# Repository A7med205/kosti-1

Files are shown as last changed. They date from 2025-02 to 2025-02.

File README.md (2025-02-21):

KOSTI-1 is a 5 DOF open-source robotic arm with a maximum payload of 500G, a reach of approximately 55cm and a total part cost of around $700; the arm lies in the mid-range between small servo arms and multi thousand dollar projects and is generally aimed towards educational and hobby purposes, but you might be able to come up with some practical ones (e.g., simple pick and place tasks, remotely turning on your coffee machine).

The manual (includes bill of material and assembly guide), .stl files, example-code and CAD files are all available for download.

*Note: The gripper displayed below is different from the updated one in the files.

[Thingiverse link](https://www.thingiverse.com/thing:6147832)

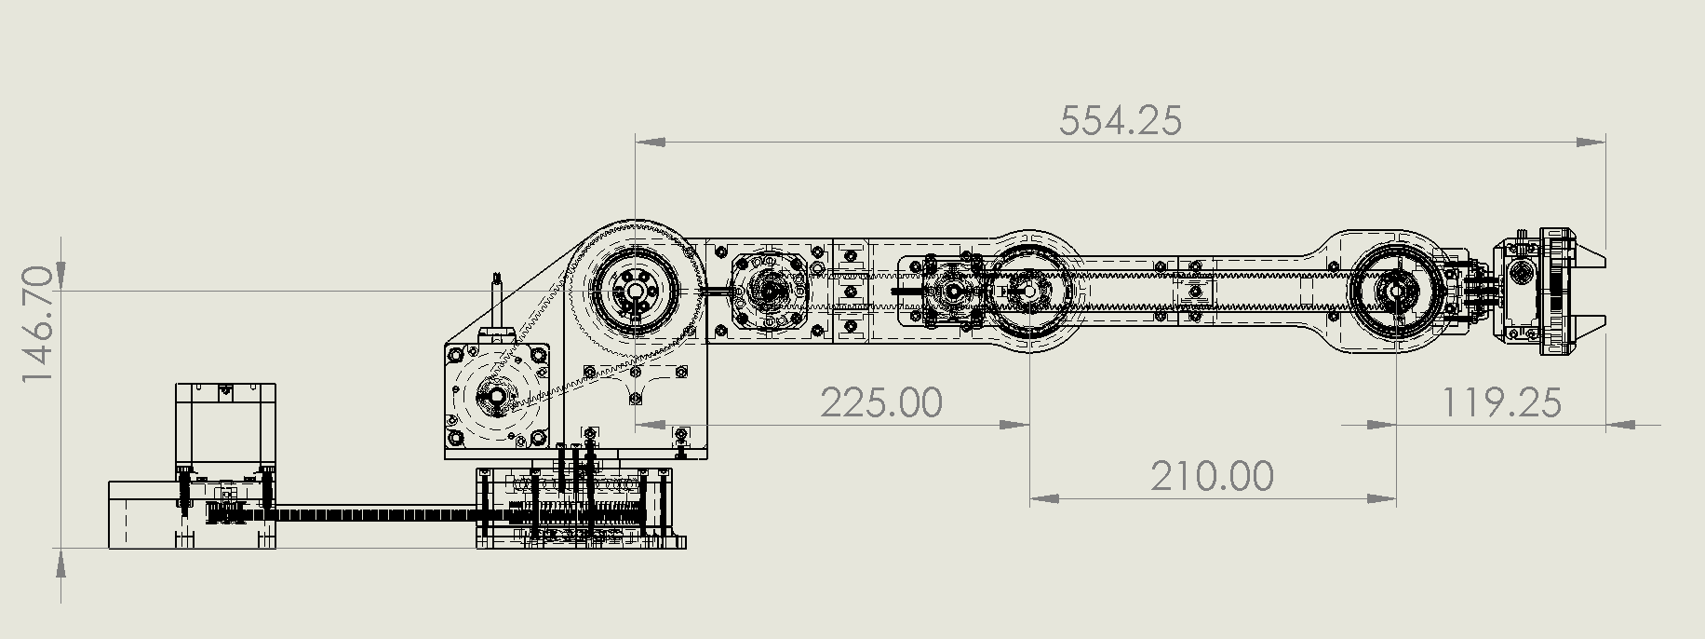
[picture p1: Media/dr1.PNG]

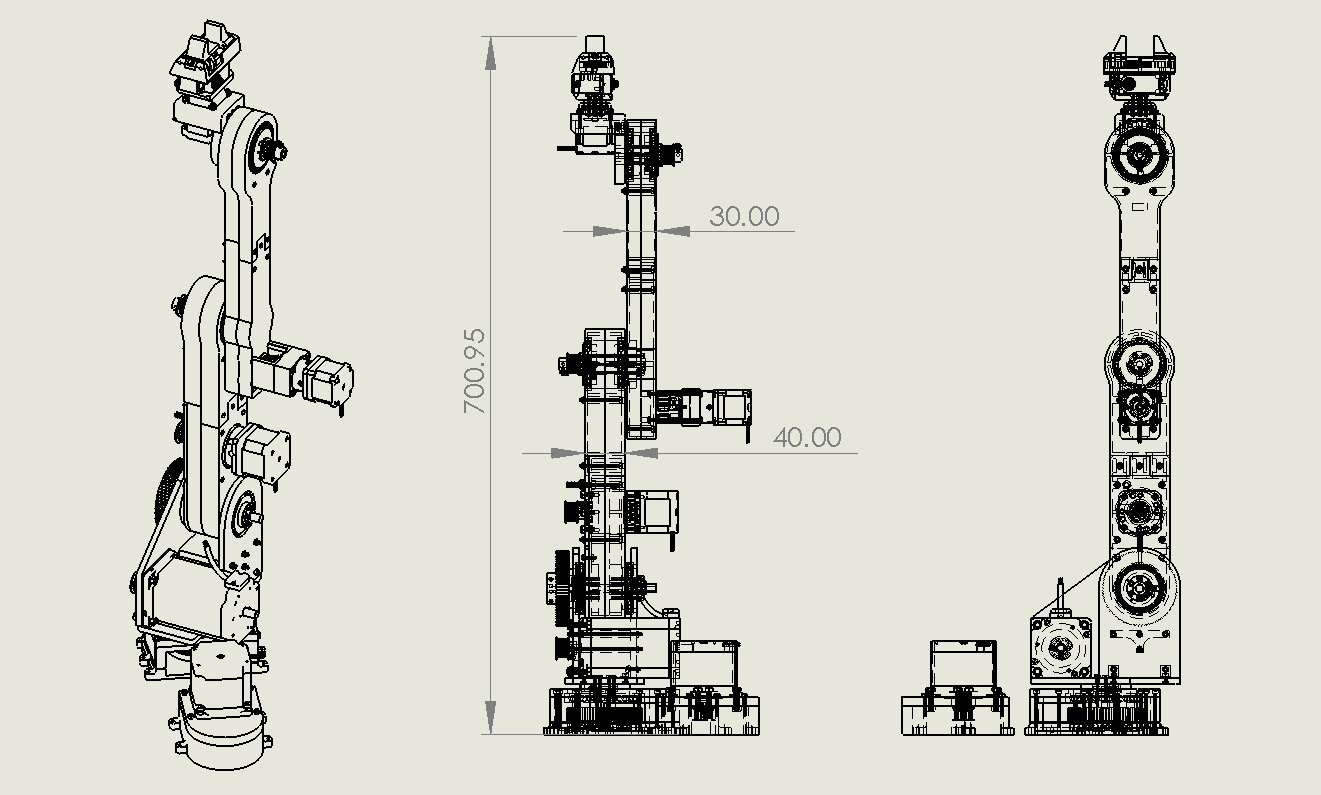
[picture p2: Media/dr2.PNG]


## Things That Might Set This Arm Apart From Other Similar Ones:

1.	Rigidity: Most parts are 3D printed, but the shoulder and base are partially made out of CNC aluminium, which adds to the rigidity of the design.
2.	Backlash: No gearbox needed for the base and shoulder joints, which means zero backlash at those joints.
3.	Smoothness: Running the shoulder and base joints at quarter step settings, combined with the fact that the remaining joints have commercial gearboxes with large resolutions, can lead to very smooth movement.
4.	Customizability: The design is entirely functional which makes it easy to modify; for instance, links can be lengthened or shortened, actuators can be replaced or modified, etc.

## Reasons Why You Might Want To Look Elsewhere:

1.	This arm isn’t entirely cost optimised; the commercial pulleys and gearboxes can be replaced with 3D printed ones or even be replaced with more affordable options, but further prototyping would be needed to achieve that.
2.	This arm is not the best choice if you want something to reliably carry out practical tasks, and there are likely commercial options out there that better suited for this.
3.	The arm uses open-loop stepper motors, and I haven’t added limit switches yet, meaning that the arm would need a pre known starting pose for every new run.

## Demo


## ROS + Moveit
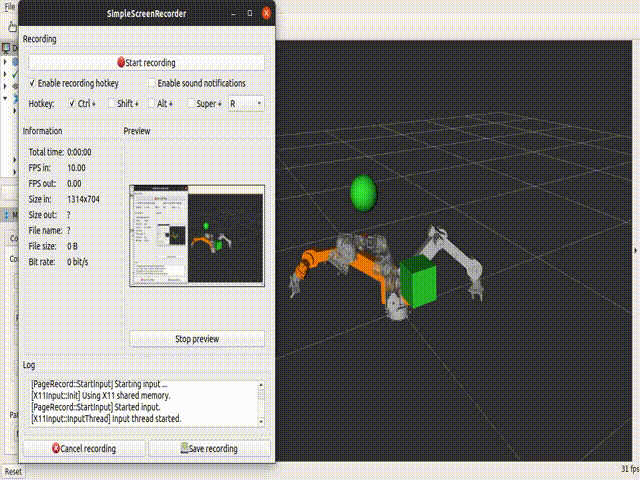
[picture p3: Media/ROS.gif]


## Assembly
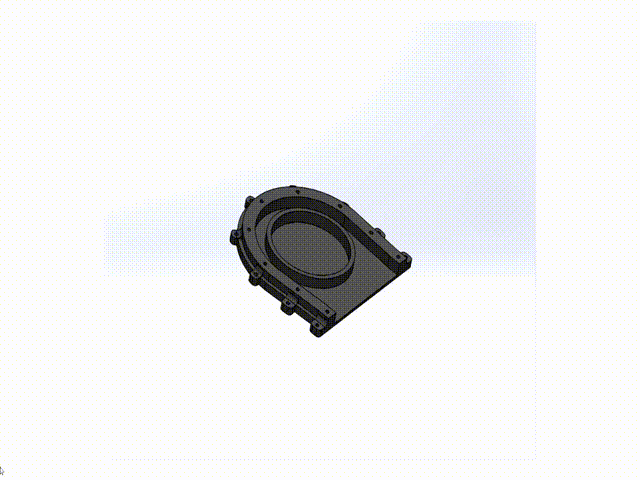
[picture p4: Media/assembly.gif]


## Exploded View
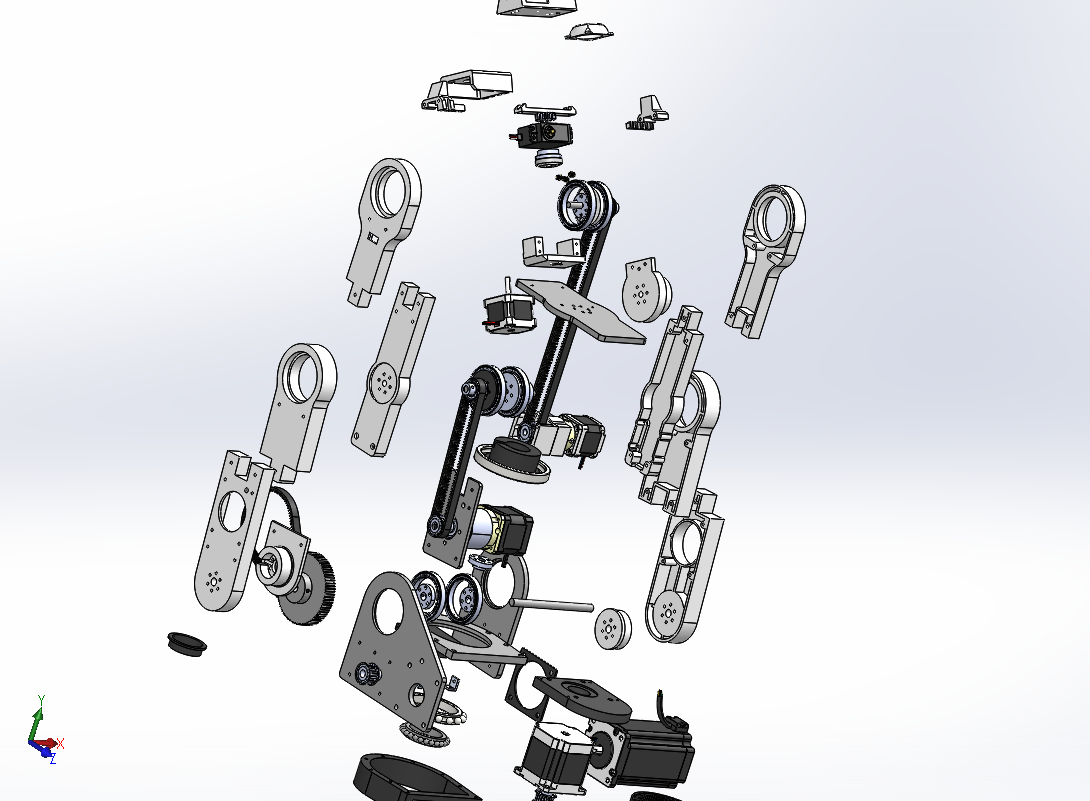
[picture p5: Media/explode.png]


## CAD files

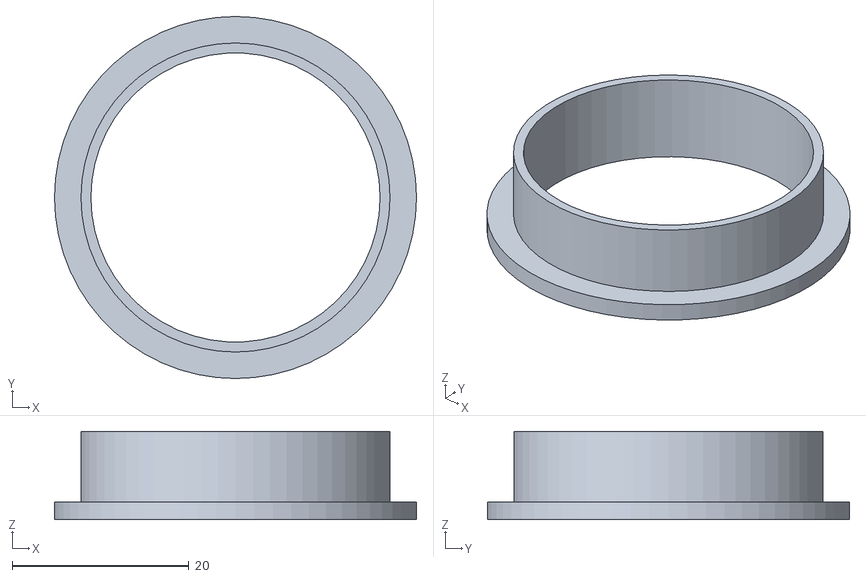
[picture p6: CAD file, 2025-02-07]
.stl files/1-stationary_base/plastic_hub.STL
41.0 x 41.0 x 10.0

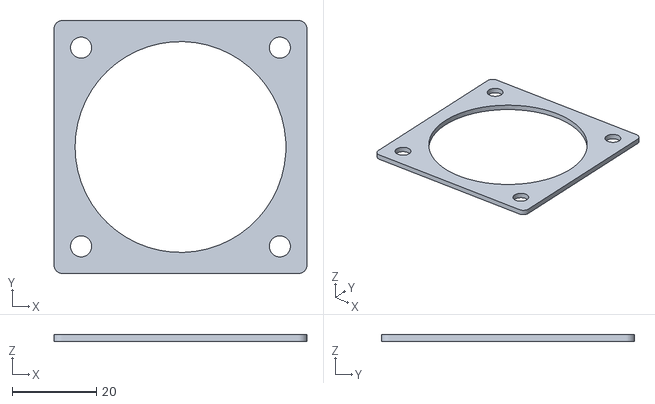
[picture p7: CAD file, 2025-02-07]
.stl files/2-rotating_base/nema24_spacer.STL
60.0 x 60.0 x 1.60

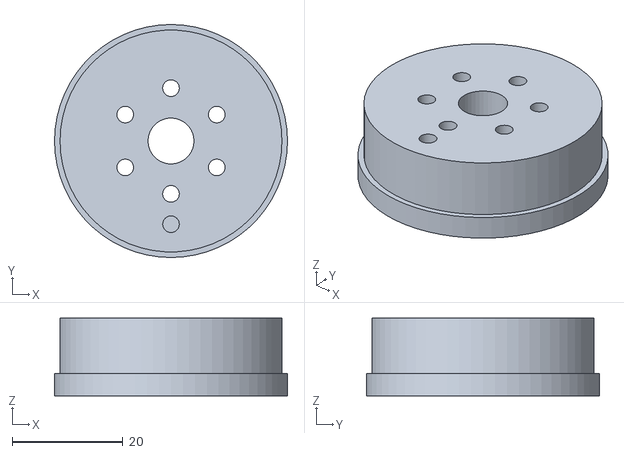
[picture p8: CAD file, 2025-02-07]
.stl files/3-lower_link/j2_hub2.STL
42.0 x 42.0 x 14.0

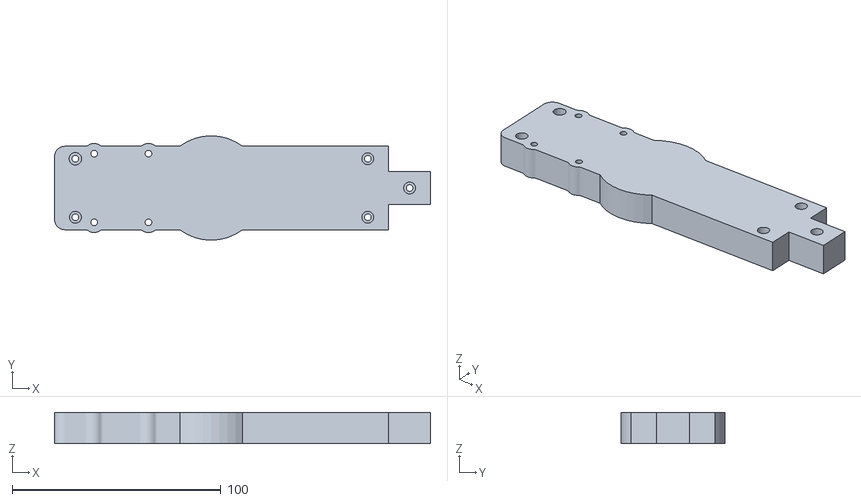
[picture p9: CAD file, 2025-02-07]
.stl files/4-middle_link/upper_arm_right_1.STL
180.0 x 50.0 x 15.0

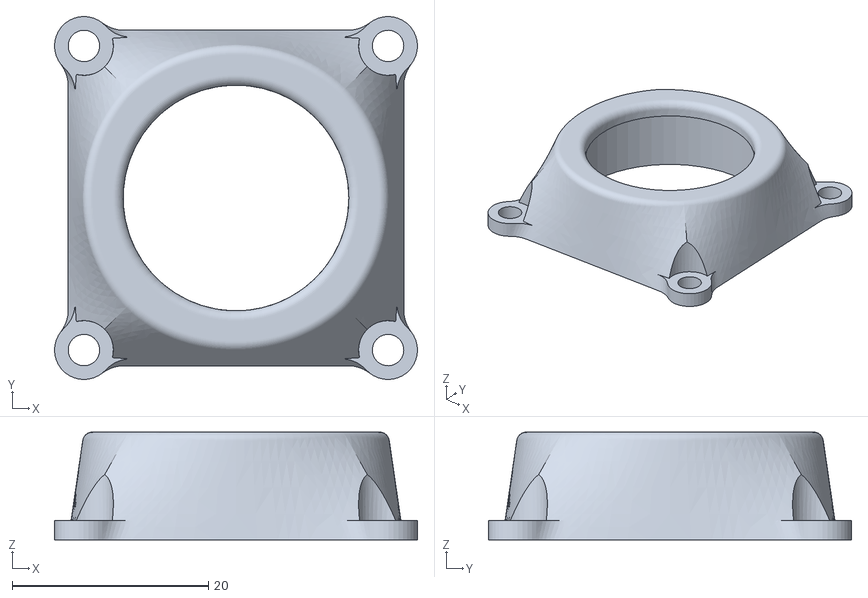
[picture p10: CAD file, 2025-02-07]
.stl files/5-third_link/bearing_housing.STL
37.0 x 37.0 x 11.0

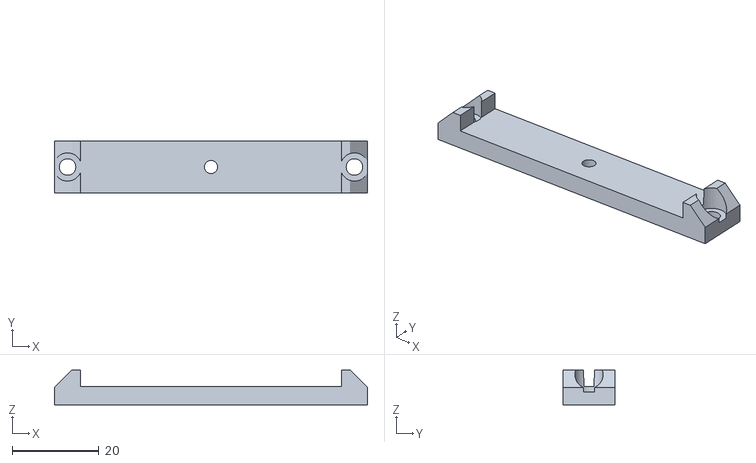
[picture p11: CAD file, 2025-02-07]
.stl files/6-end_effector_SG1/SG1_center_bar.STL
72.0 x 12.0 x 8.02

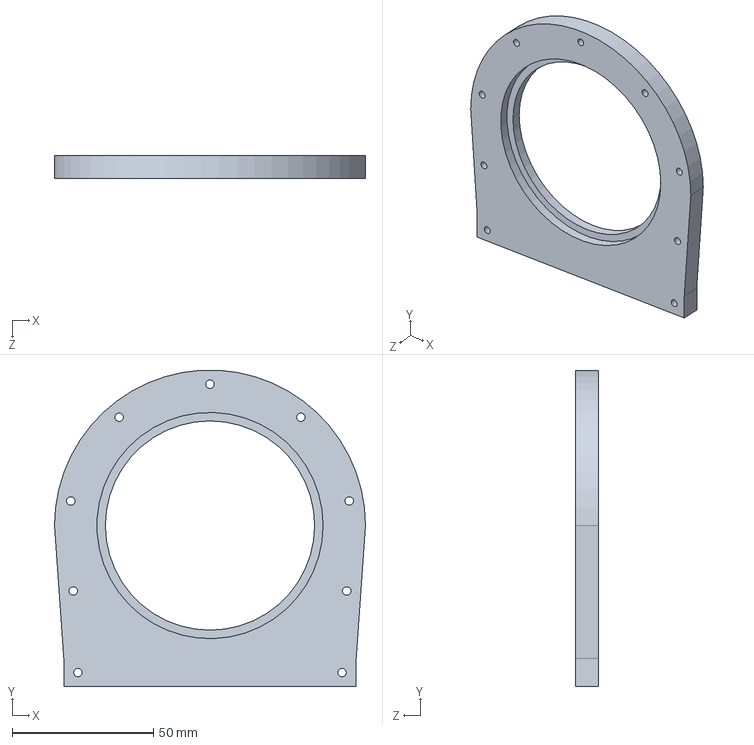
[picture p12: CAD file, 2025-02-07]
Aluminium Parts/aluminum base.SLDPRT
110.0 x 111.9 x 8.00 mm

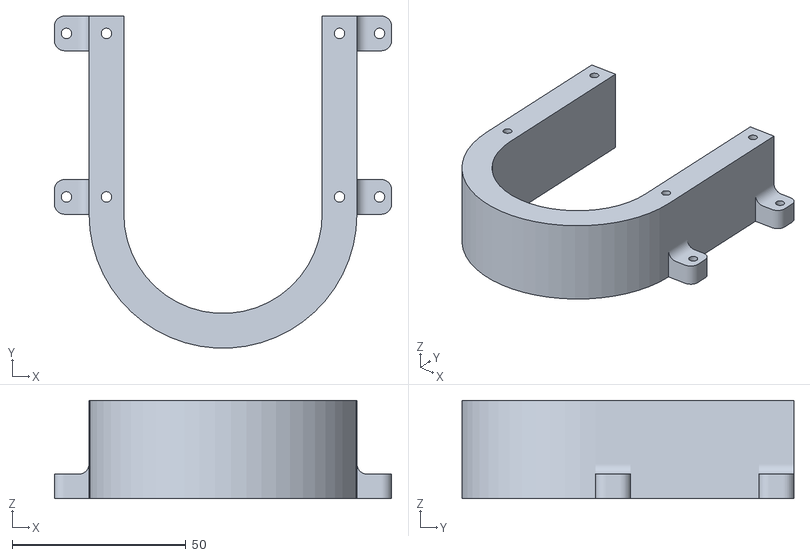
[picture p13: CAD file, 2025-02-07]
.stl files/1-stationary_base/j1_2.STL
97.0 x 95.4 x 28.2

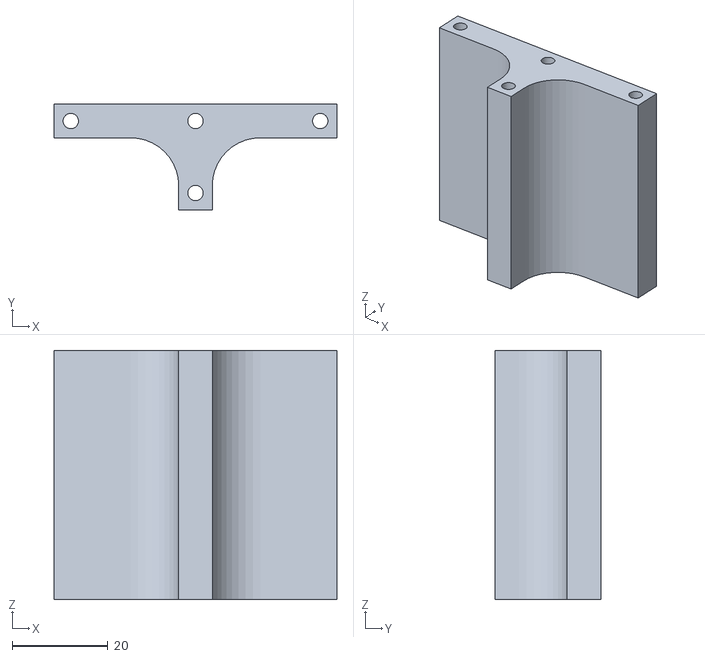
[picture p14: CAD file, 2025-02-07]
.stl files/2-rotating_base/support.STL
59.0 x 22.0 x 52.0

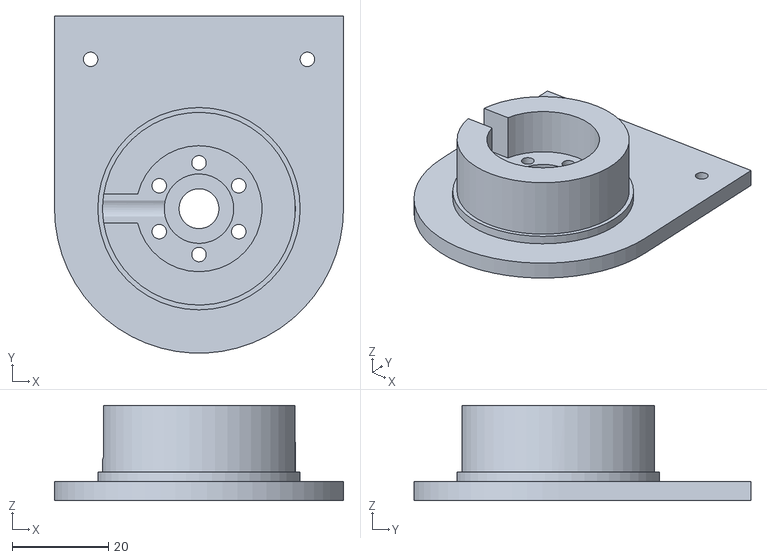
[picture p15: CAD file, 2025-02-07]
.stl files/3-lower_link/j2_hub1.STL
60.0 x 70.0 x 19.8

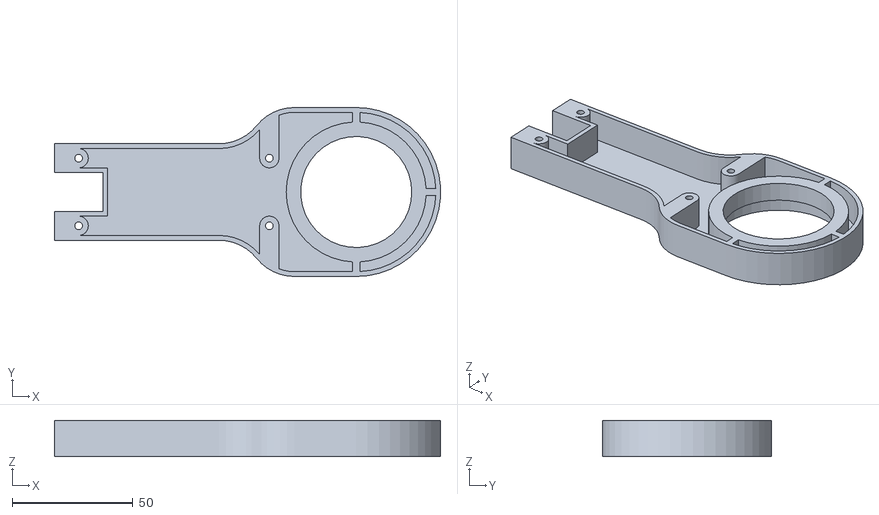
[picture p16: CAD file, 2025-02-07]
.stl files/4-middle_link/upper_arm_right_2.STL
159.9 x 70.0 x 15.0

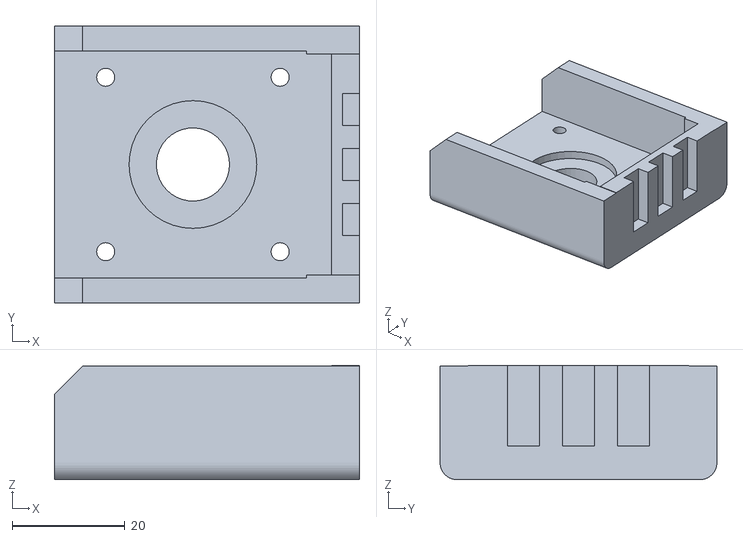
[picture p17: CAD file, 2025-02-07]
.stl files/5-third_link/link3.STL
54.2 x 49.2 x 20.3

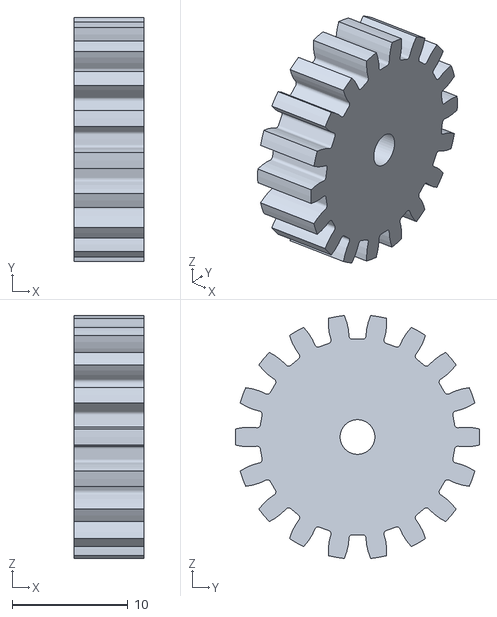
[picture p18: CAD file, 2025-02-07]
.stl files/6-end_effector_SG1/SG1_gear.STL
6.00 x 21.1 x 21.0

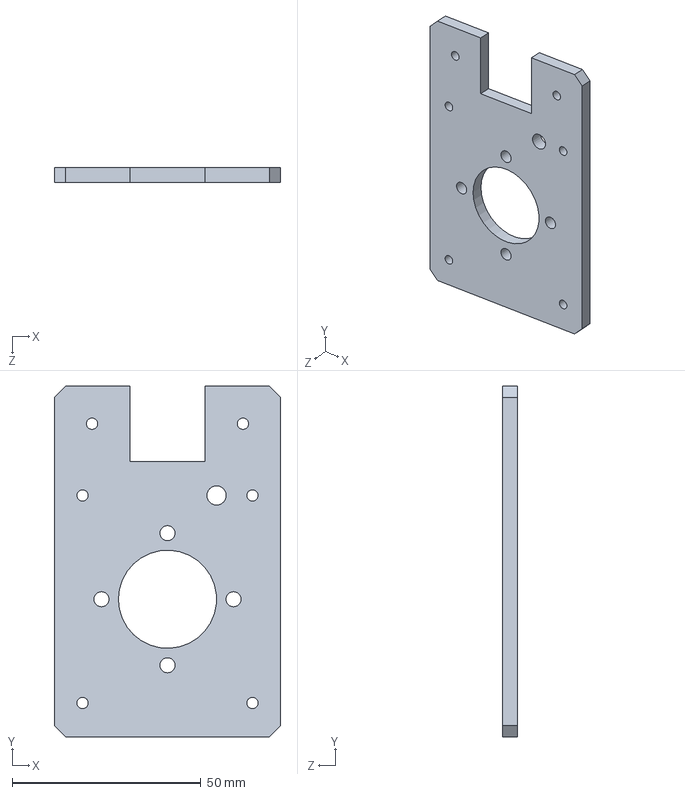
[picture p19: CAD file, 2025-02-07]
Aluminium Parts/j3_plate.SLDPRT
60.0 x 93.0 x 4.00 mm

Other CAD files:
.stl files/1-stationary_base/j1_1.STL
.stl files/2-rotating_base/j1_hub.STL
.stl files/3-lower_link/lower_arm_right_2.STL
.stl files/4-middle_link/j4_mount_2.STL
.stl files/1-stationary_base/ground.STL
.stl files/1-stationary_base/stationary_base.STL
.stl files/3-lower_link/lower_arm_left_1_.STL
.stl files/3-lower_link/lower_arm_left_2.STL
.stl files/3-lower_link/lower_arm_right_1_.STL
.stl files/4-middle_link/J3_hub_2.STL
.stl files/4-middle_link/clamp.STL
.stl files/4-middle_link/clamp2.STL
.stl files/4-middle_link/j3_hub.STL
.stl files/4-middle_link/j4_mount.STL
.stl files/4-middle_link/upper_arm_left_1_.STL
.stl files/4-middle_link/upper_arm_left_2.STL
.stl files/5-third_link/bearing_housing_2.STL
.stl files/5-third_link/end_effector_hub.STL
.stl files/5-third_link/end_effector_hub2.STL
.stl files/5-third_link/j4_hub1.STL
.stl files/5-third_link/j4_hub2.STL
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

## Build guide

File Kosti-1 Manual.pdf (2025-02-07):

## KOSTI-1 Manual

# Kosti-1 Manual

Features:

Kosti-1 is a 5 degree of freedom open-source robotic arm with a maximum payload of 500gm (including the end-effector) and a reach of approximately 55cm. The total part cost is around $700 in addition to machining and shipping costs.

The body of the arm requires both 3D-printed parts and aluminium parts that need to be machined and can’t be omitted without significant design changes. All joints are driven by open-loop stepper motors, and 4 out of 5 of these joints have a timing belt and pulley drive for load reduction and/or power transmission. This manual includes schematics and examples for Arduino based control, but different methods of control can be employed.

CONTENTS:

- 3D Printing
- CNC Machining
- Post Machining
- Arm Platform
- Tools
- Fits and Tolerances
- Belt Tensioning
- End Effector
- Bill of Materials
- Assembly Guide
- Stepper Motor Wiring
- Servo Gripper Wiring

3D Printing the Parts:

Printer: All parts can fit inside a 220x220mm printer.

Filament: The design of the plastic parts assumes a shrinkage rate of no more than 2-3%, which is common for PLA, take that into consideration if you end up using another type of filament and consider printing a single piece first to check the fits before proceeding with the rest.

Printer settings: All parts were printed using 0.2mm layer, height and 20-25% infill and two outer shells; increasing the number of shells can add rigidity but would add to the weight. Make sure that you pick the print orientation that minimizes support material for each part.

CNC Machining:

There are 5 parts that need to be machined out of aluminium plate(s) using a CNC machine; the 3 maximum dimensions for each part are (131 x 82 x 6mm), (131 x 148.17 x 6mm), (150.20 x 64 x 6mm), (112 x 110 x 8mm) and (93 x 60 x 4mm), you can use these dimensions to select the stock plate.

Post Machining:

Shafts: An 8mm shaft needs to be cut into an 8x47mm one and an 8x110 one, and a 6mm shaft needs to be cut into a 6x95mm one and a 6x64mm one. A 0.5mm flat should be filed onto the 8x110mm and 6x95mm shafts for more secure joints, and optionally, the same can be done for the other two shafts.

Pulleys: The bore on two out of the six small pulleys needs to be increased in diameter from 6mm to 8mm to match the motor shafts, and ideally, a lathe would be used to do this, similar to what’s done here. (https://www.youtube.com/watch?v=ZHTQ478ji7k) Other methods can be used with less precise results.

Threaded Rods: Four M3x75mm and four M3x55mm threaded rods need to be cut out of standards lengths ones.

M5 Screws: If narrow head M5 screws are not available, eight hex head ones can be filed to fit on the back of the face of the Nema24 and Nema23 motors.

‘link3’: Three M3 clearance holes need to be drilled into this part, see step NO. 36.

Platform: You are likely going to need to prepare some sort of platform, usually out of wood, to secure the base of the arm onto.

Tools:

The tools you need would depend, in some cases, on your preferred method of machining; you might want to cut the shafts with a hacksaw or a circular saw, you might have a mill for filing the flats or you might just use a file and a vise, and you might have a lathe for boring the pulleys or you might use a drill with a reamer bit. You will need a soldering iron, 1.5mm, 2mm and 2.5mm Allen keys, and some pliers.

Fits and Tolerances:

The CAD files included for aluminium parts have bearing and screw holes that simply match the nominal diameters of the ready parts, these can be edited to achieve the desired fit.

The bearing and screw-clearance holes on the 3D printed parts assume a shrinkage rate of 2-3%, if the fit on the test piece fails one way or the other, the .stl file can be slightly scaled up or down using the slicing application; make sure that use uniform scaling.

The screw holes on the printed parts match the diameter of the screw shafts and should shrink enough for the screws to self-tap into.

Belt Tensioning:

Base joint: The base is split into two fixed parts connected only by the belt; these two parts can be manually set apart and secured to the platform with a distance that ensures that the belt is properly tensioned.

Shoulder joint: The centre distance required for good tension between each two pulleys can be calculated using the provider’s online tool, and the centre distance on the aluminium plate holding the two pulleys for the shoulder joint is 1% larger than the calculated one, which would result in good tension at installation without the need for a tensioner, assuming that the specified closed loop belt and pulleys are selected. In any case, a clearance hole for an M5 screw is present on the plate behind where the belt should be, and that hole can be used to add a tensioner similar the one included for the elbow joint and explained below.

Elbow joint: There’s no easy way to predict the resulting centre distance on 3D printed parts, and proper tension can be hard to achieve, even when allowance is made for shrinkage, without some sort of adjustable tensioner;
the tensioner for the elbow joint is | simply two 5mm bore bearings with a
thickness of 5mm held on an M5 | screw and secured with nuts on both sides, the
thickness of the bolt below the | bearings can be filed down if they’re too high
and a spacer can be added if they’re | too low, and the tension can be adjusted by
either 3D printing a small hollow | cylinder that goes over the bearings or by
using bearings with a larger outer | diameter. See assembly step NO. 13.

Wrist Joint: The second link where the wrist joint belt is attached wasn’t designed to hold a screw based tensioner, and I currently don’t have access to the assembly to test another tensioner design, consequently, the recommended method for tensioning the upper most belt is cutting it and attaching the two ends with two clamps (.stl included), a screw and a nut. The wrist joint should have more than the sufficient range of motion without the clamp reaching either pulley, but you’re free to come up with other ways for tensioning this belt.

End Effector:

The end effector included is the open-source gripper from Anninrobotics.com; the assembly manual and bill of materials for the servo gripper are separately available at anninrobotics.com/downloads under ‘Servo Gripper’, but the printable files have been adjusted to fit onto the different hub and can be found with the rest of Kosti-1’s files. Note that the same servo is included in both Kosti-1’s BOM and the BOM for the gripper while you will only need one servo.

Bill of Materials:

NO. | PART NAME | QTY. | NOTE | LINK
| Belts & Pulleys
1 | 80T Pulley, 3 mm Pitch, 8mm Bore | 2 | | Link (https://shop.sdp-si.com/catalog/product/?id=A_6A53M080NF0908)
2 | 20T Pulley, 3 mm Pitch, 6mm Bore | 6 | | Link (https://shop.sdp-si.com/catalog/product/?id=A_6A53M020DF0906)
3 | 184T, 3mm pitch, 9mm width Belt | 1 | | Link (http://shop.sdp-si.com/catalog/product/?id=A%206R53M184090)
4 | 119T, 3mm pitch, 9mm width Belt | 1 | | Link (http://shop.sdp-si.com/catalog/product/?id=A%206R53M119090)
5 | 118T, 3mm pitch, 9mm width Belt | 1 | | Link (http://shop.sdp-si.com/catalog/product/?id=A%206R53M118090)
6 | 187T, 3mm pitch, 9mm width Belt | 1 | | Link (http://shop.sdp-si.com/catalog/product/?id=A%206R53M187090)
| Motors
7 | Nema24 4.2A 4Nm | 1 | | Link (https://www.omc-stepperonline.com/dual-shaft-nema-24-stepper-motor-4-2a-4nm-566-oz-in-60x60x100mm-4-wires-24hs39-4204d)
8 | Nema23 2.8A 1.26Nm | 1 | | Link (https://www.omc-stepperonline.com/nema-23-bipolar-1-26nm-178-4oz-in-2-8a-2-5v-57x56mm-4-wires-6mm-shaft-23hs22-2804s1)
9 | Nema17 Geared | 1 | | Link (https://www.omc-stepperonline.com/nema-17-stepper-motor-l-40mm-gear-ratio-20-1-mg-series-planetary-gearbox-17hs15-1584s-mg20)
10 | Nema14 Geared | 1 | | Link (https://www.omc-stepperonline.com/nema-14-stepper-motor-bipolar-l-33mm-w-gear-ratio-19-1-planetary-gearbox-14hs13-0804s-pg19)
11 | Nema16 | 1 | | Link (https://www.omc-stepperonline.com/nema-16-bipolar-1-8deg-21ncm-29-7oz-in-0-4a-12v-39x39x34mm-4-wires-16hs13-0404s)
| Electronics
12 | Servo | 1 | | Link (https://www.amazon.com/ANNIMOS-Digital-Waterproof-Crawler-Control/dp/B07GK1G5FV?amp;keywords=25kg+servo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)
13 | arduino | 1 | | Link (https://www.amazon.com/ELEGOO-ATmega2560-ATMEGA16U2-Arduino-Compliant/dp/B01H4ZDYCE?amp;keywords=arduino%252Bmega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)
14 | jumper wires | 35 | | Link (https://www.amazon.com/sspa/click?linkId=0729893a4c66a6ac7699d003874922f6&camp=1789&creative=9325)
15 | bread board | 1 | | Link (https://www.amazon.com/Pcs-MCIGICM-Points-Solderless-Breadboard/dp/B07PCJP9DY?amp;keywords=breadboard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)
16 | extension wires | 8 | | Link (https://www.omc-stepperonline.com/stepper-motor-4-wires-400mm-cable-with-pitch-connector-c001)
17 | DM54T driver | 2 | | Link (https://www.omc-stepperonline.com/digital-stepper-driver-1-0-4-2a-20-50vdc-for-nema-17-23-24-stepper-motor-dm542t)
18 | DM320T driver | 3 | | Link (https://www.omc-stepperonline.com/digital-stepper-driver-0-3-2-2a-10-30vdc-for-nema-8-11-14-16-17-stepper-motor-dm320t)
19 | 400W 24V power supply | 1 | | Link (https://www.omc-stepperonline.com/nema-16-bipolar-1-8deg-21ncm-29-7oz-in-0-4a-12v-39x39x34mm-4-wires-16hs13-0404s)
| Bearings
20 | 35x62x9mm_bearing_16007 | 1 | | Link (https://www.amazon.com/16007-Bearing-grove-bearing-Radial/dp/B07LB84RHP?amp;keywords=35x62x9+bearing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)
21 | 50x80x10mm_bearing_16010 | 1 | | Link (https://www.amazon.com/16010-Open-Bearing-50x80x10-Shipping/dp/B083QPRJZ6?amp;keywords=50x80x10+bearing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)
22 | 40x52x7mm_bearing_6808-2RS | 6 | | Link (https://www.amazon.com/XIKE-6808-2RS-Bearings-40x52x7mm-Pre-Lubricated/dp/B09D2VY3BK?amp;keywords=40x52x7%252Bbearing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)
23 | 20x27x4mm_bearing_6704ZZ | 1 | | Link (https://www.amazon.com/uxcell-6704ZZ-Groove-Bearings-Shielded/dp/B082PSMMGV?amp;keywords=20x27x4mm%252Bbearing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)
24 | 5mm ID 5mm thick bearing | 2
| Fastners, Shafts & Hubs
25 | M3 x 0.5 x 10 Hex | 6 | | Link (https://www.amazon.com/Assortment-Stainless-Replacement-Machine-Fastener/dp/B0BMQFHDBH?amp;keywords=M3+Hex+Cap+Screws+set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)
26 | M3 x 0.5 x 35 Hex | 9
27 | M3 x 0.5 x 12 Hex | 6
28 | M3 x 0.5 x 8 Hex | 8
29 | M3 x 0.5 x 25 Hex | 14
30 | M3 x 0.5 x 5 Hex | 12
31 | M3 x 0.5 x 40 Hex | 12

32 | M3 x 0.5 x 30 Hex | 19
33 | M3 x 0.5 x 20 Hex | 8
34 | M3 x 0.5 x 16 Hex | 4
35 | M3 x 0.5 x __ Hex | 13 + 12
36 | Hex nut, M3 x 0.5 | 42 + 13 + 12
37 | M4 x 0.7 x 10 | 4
38 | M5 screw x 0.8 x 20 | 8 | Link (https://www.amazon.com/Kadrick-Assortment-Metric-Washers-Upgrade/dp/B0BZ6NVQZP?amp;qid=1689360725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)
39 | M5 screw x 0.8 x 25 | 1
40 | M5 nut, M5 x 0.8 | 10
41 | Corner Bracket | 4 | Link (https://www.mcmaster.com/1959N41/)
42 | Threaded rod M3 x 0.5 x (75 + 55) | 4 | Link (https://www.amazon.com/uxcell-130mm-Threaded-Stainless-Threads/dp/B094H9VQDB?amp;qid=1689358986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)
43 | M3 Insert | 3 | Link (https://www.amazon.com/Printing-M3x4x5mm-Threaded-Embedment-Automotive/dp/B0BTYF2MMD?amp;qid=1689358986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)
44 | Shaft 1, 2_8 x (47+110) | 1 | Link (https://www.amazon.com/uxcell-200mm-Stainless-Steel-Solid/dp/B082ZNFMXV?amp;qid=1689353881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)
45 | Shaft 3, 4_6 x (95 +64) | 1 | Link (https://www.amazon.com/6mmX100mm-Linear-Motion-Shaft-Diameter/dp/B08HYF2WPX?amp;keywords=6mm%252Bshaft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)
46 | 8mm hub | 3 | Link (https://www.pololu.com/product/2693)
47 | 6mm hub | 3 | Link (https://www.pololu.com/product/1999/)
48 | 5mm hub | 1 | Link (https://www.pololu.com/product/1998)
*Some of these are affiliate links.
*You can source the same parts from any preferred distributer.

Assembly Guide:
*Some parts are supressed when they’re not the focus of a given step.

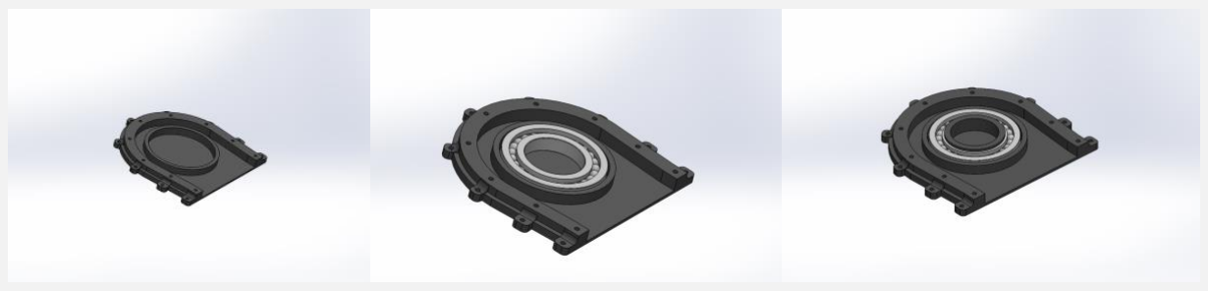
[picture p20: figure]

1. Insert the 35mm bore bearing into the piece making the bottom of the base and insert the ‘plastic_hub’ piece into the bearing; the bearing should have a slide fit.
2. Insert the 8x47mm shaft into the 8mm aluminium hub, making sure that the end of the shaft is flat with the surface of the hub and secure the shaft to the hub using the M3x10mm socket head screw instead of the set screw. Install the remaining hub set screw normally.

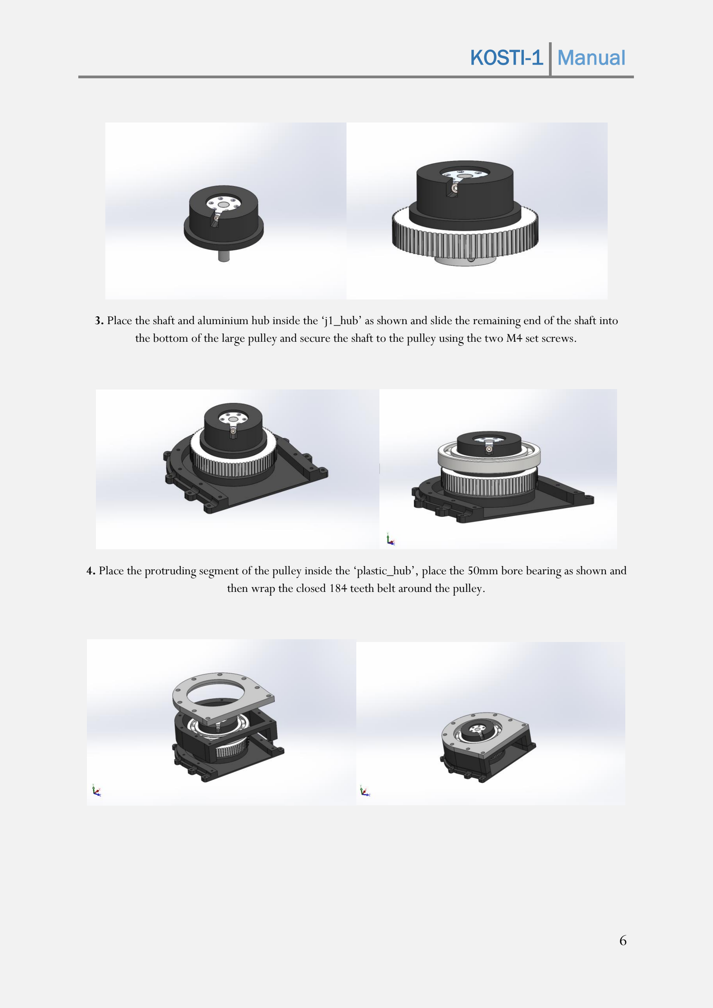
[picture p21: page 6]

3. Place the shaft and aluminium hub inside the ‘j1_hub’ as shown and slide the remaining end of the shaft into the bottom of the large pulley and secure the shaft to the pulley using the two M4 set screws.
4. Place the protruding segment of the pulley inside the ‘plastic_hub’, place the 50mm bore bearing as shown and then wrap the closed 184 teeth belt around the pulley.

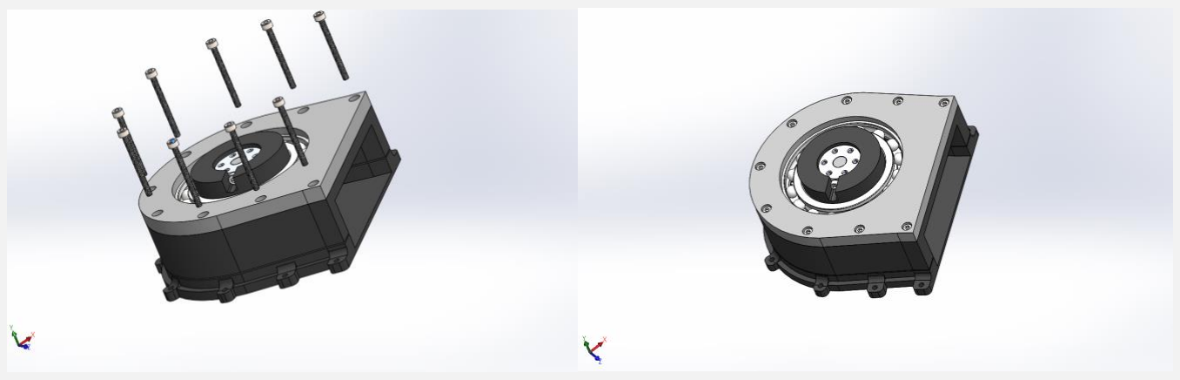
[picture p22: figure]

5. Complete the base by placing the two remaining plastic and aluminium pieces over the large bearing as shown and screwing everything using 9 M3x35mm socket head screws; the bearing should have a slide fit; note that the screws should self-tap into the bottom piece.
6. Secure the aluminium ‘base_plate’ and ‘left-plate’ using two corner brackets, two M3x12mm screws, two M3x8mm screws and 4 M3 nuts; note that the longer screws go into the side plate and that the longer side of the bracket should be the vertical one.

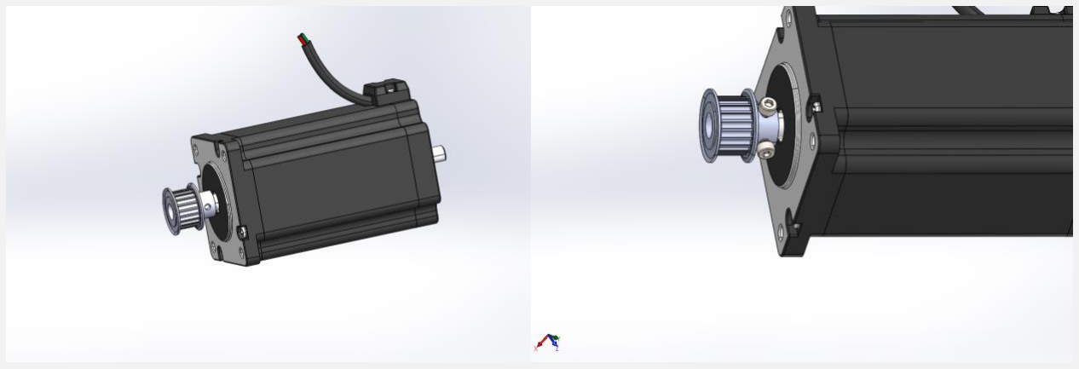
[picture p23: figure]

7. Secure the small 8mm bore onto the Nema24 motor using two 5mm screws, making sure that screws are pressing on the flat sides of the shaft and that the pulley is as close to the body of the motor as possible without the screws leaving the flat sides.

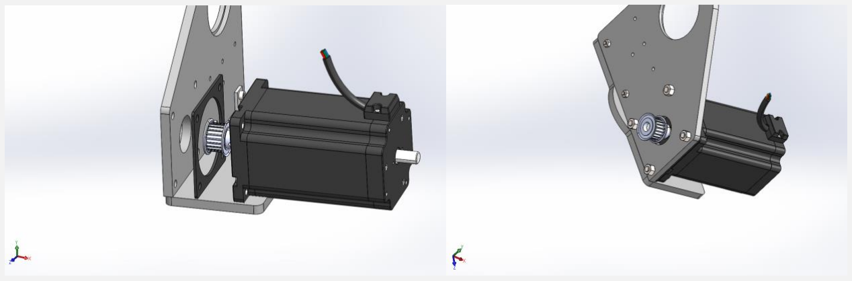
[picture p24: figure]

8. Secure the Nema24 motor to the side plate, through the spacer, using 4 M5x20mm screws and 4 M5 nuts.
9. Secure the plates and the motor to the base using 6 M3x25mm screws; the screws should go through the threaded 8mm hub below and self-tap into the plastic, so make sure that the 6 holes on the hub and plate are properly aligned.

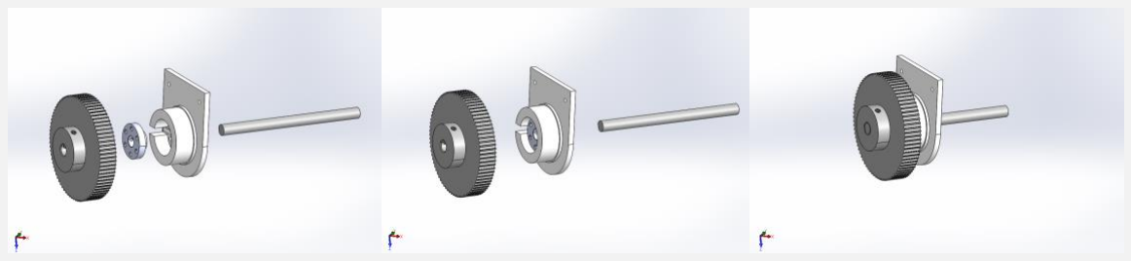
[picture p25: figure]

10. Insert the 8mm aluminium hub into ‘j2_hub1’ as shown, with the set screw holes facing the removed part of the plastic cylinder, and slide the 8x110mm shaft through a large pulley that’s held flat against ‘j2_hub1’, making sure that the end of the shaft is flat with the surface of the pulley. The pulley shouldn’t be secured yet and is only needed to mark the shaft distance.
11. Secure the shaft to the hub using an M3x10mm screw and remove the pulley.

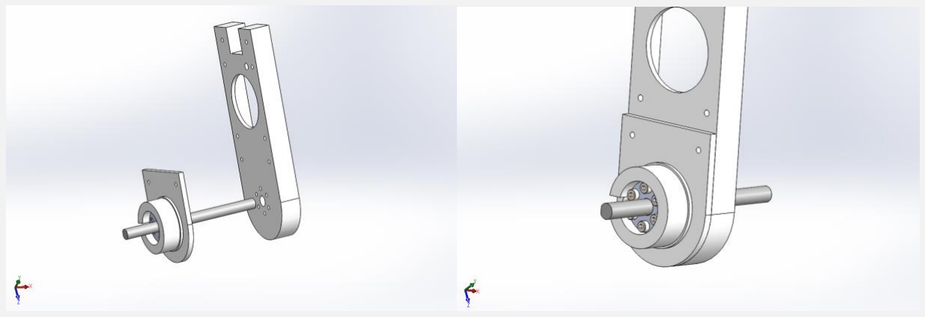
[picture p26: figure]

12. Install the ‘j2_hub’ and the shaft to ‘lower_arm_left_1’ using 6 M3x25mm screws that should go through the aluminium hub and self-tap into the arm.

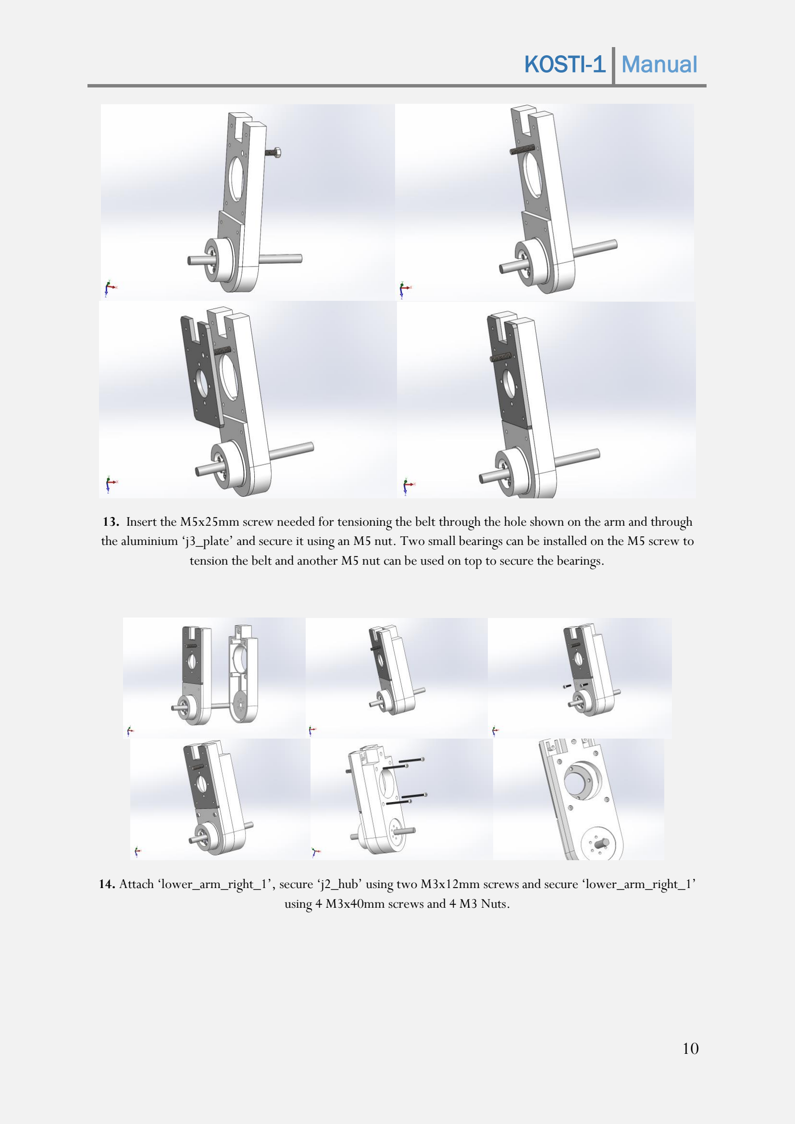
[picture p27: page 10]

13. Insert the M5x25mm screw needed for tensioning the belt through the hole shown on the arm and through the aluminium ‘j3_plate’ and secure it using an M5 nut. Two small bearings can be installed on the M5 screw to tension the belt and another M5 nut can be used on top to secure the bearings.
14. Attach ‘lower_arm_right_1’, secure ‘j2_hub’ using two M3x12mm screws and secure ‘lower_arm_right_1’ using 4 M3x40mm screws and 4 M3 Nuts.

15. Attach ‘j2_hub2’ and the 8mm aluminium hub to the shaft, making sure that all holes are aligned and that set screw holes are over the flat side of the shaft, and secure the aluminium hub to the shaft using an M3x10mm screw.

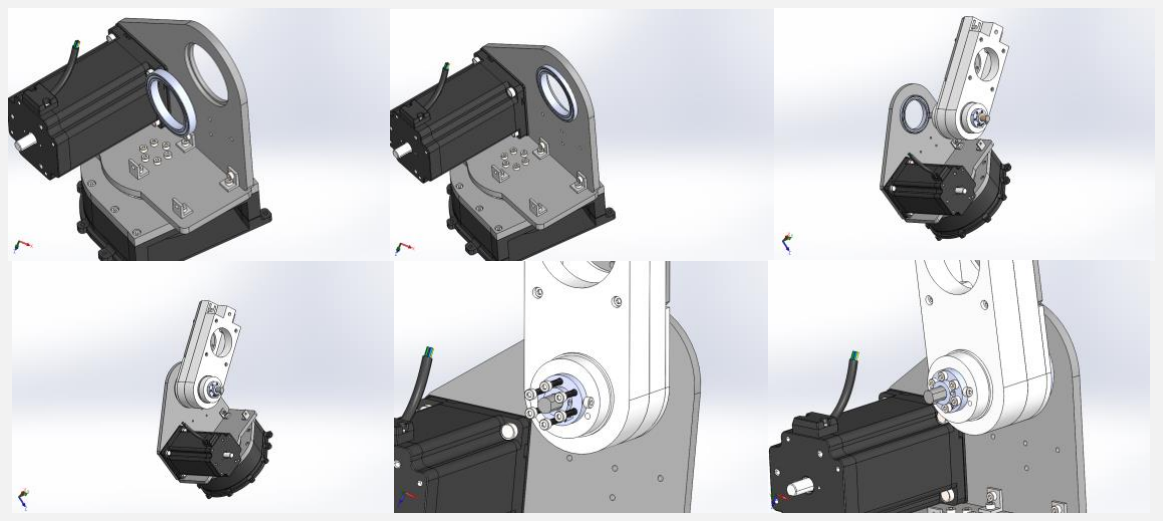
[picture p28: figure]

16. Slide the 40mm bore bearing into the designated place on the side plate, attach the assembled part of the arm as shown and secure the right aluminium hub using 6 M3x30mm screws.

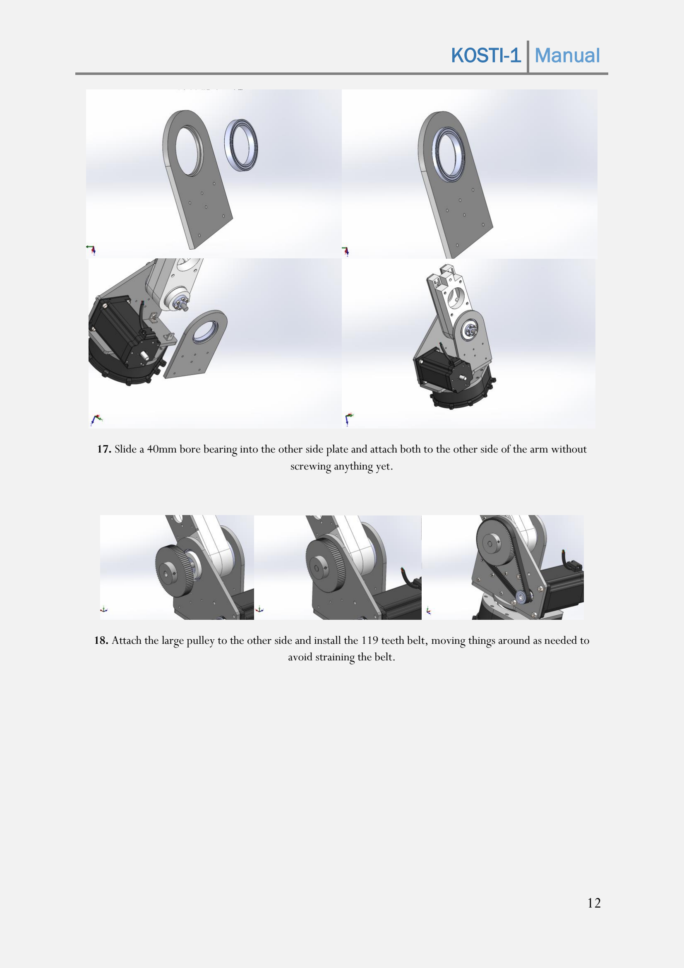
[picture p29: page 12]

17. Slide a 40mm bore bearing into the other side plate and attach both to the other side of the arm without screwing anything yet.
18. Attach the large pulley to the other side and install the 119 teeth belt, moving things around as needed to avoid straining the belt.

19. Secure the unsecured right plate using two brackets, two M3x12mm screws on the side, two M3x8mm screws on the bottom and 4 M3 nuts, similar to the left plate.
20. Slide the ‘support’ between the two plates and hold everything together using 4 M3x65mm threaded rods and 8 M3 nuts.
21. Attach ‘lower_arm_right_2’ and ‘lower_arm_left_2’ together using 2 M3x40mm screws and two nuts as shown, attach the result to the assembled half of the arm and secure these two halves using 3 M3x40mm screws and 3 nuts.

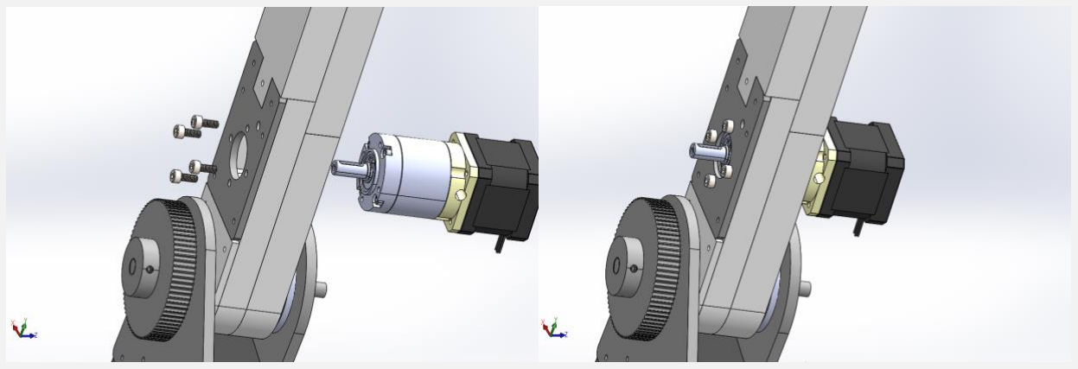
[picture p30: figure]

22. Install the geared Nema17 motor, with the motor wires pointing down using 4 M4x10mm screws.

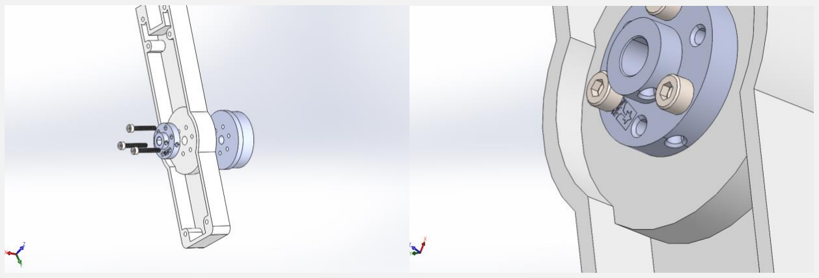
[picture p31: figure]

23. Attach the ‘J3_hub2’, ‘upper_arm_left_1’ and the 6mm aluminium hub using 3 M3x30mm screws inserted on every second hole as shown; make sure that set screw holes on the aluminium hub are facing the lower end of the arm. Note that parts ‘j3_hub’ and ‘j4_hub2’ are identical.
24. Insert the 6mm aluminium hub into ‘J3_hub1’, making sure that all holes are aligned, and slide the 6x95mm shaft through the hub followed by an M3x5mm screw and a small pulley to mark the shaft distance.

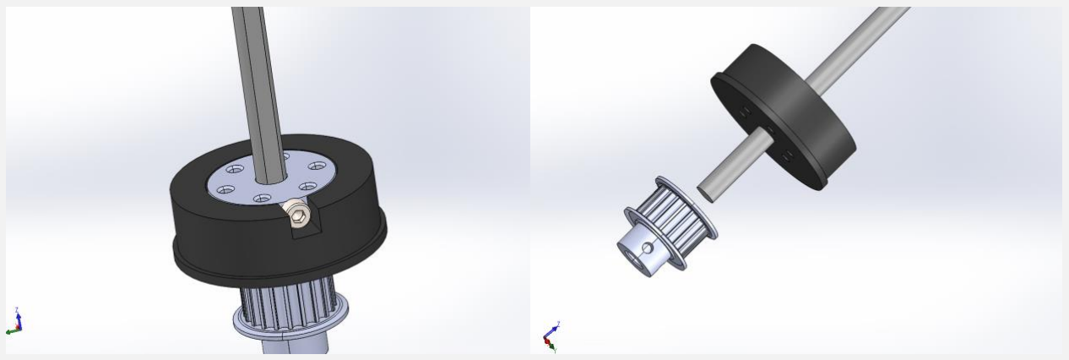
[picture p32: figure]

25. With one end of the shaft flat with the surface of the pulley, secure the shaft to the aluminium hub using an M3x12mm screw against the flat of the shaft and remove the pulley and the M3x5mm screw.

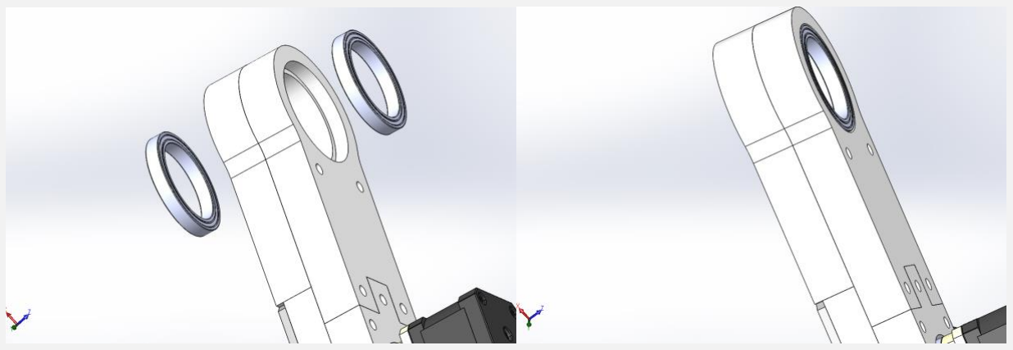
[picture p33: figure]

26. Insert two 40mm bore bearings into the upper end of the assembled arm.
27. Attach ‘J3_hub1’ and ‘J3_hub2’ together, through the bearings, using 3 M3x40mm screws, making sure that the 3 screws on the left side aren’t aligned with those on the right side, and that the flat side of the shaft is aligned with set screw holes on the right hub.

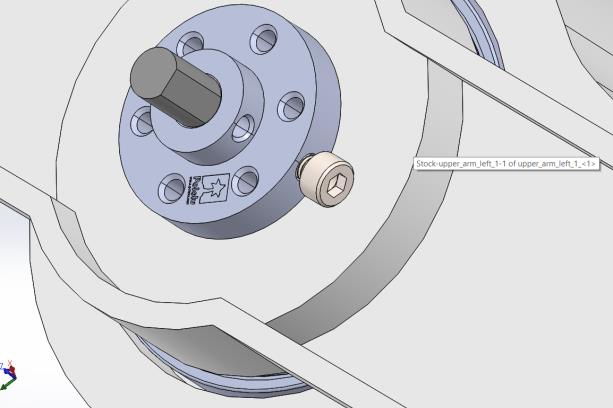
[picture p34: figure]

28. Secure the shaft to the right hub using an M3x12mm screw.

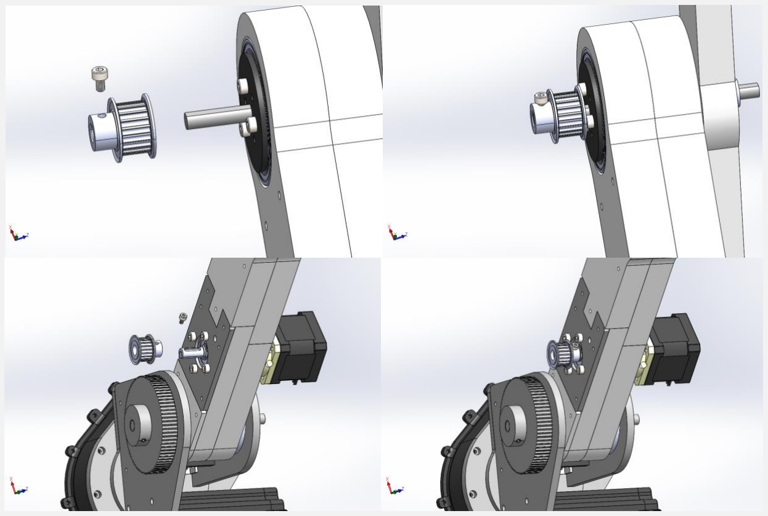
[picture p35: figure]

29. Secure a small 8mm bore pulley to the motor shaft using one M3x5mm screw through the motor shaft’s key hole, making sure that the pulley is as close as possible to the motor’s body, and secure a small 6mm bore pulley to the upper shaft using two M3x5mm screws, with one of the two screws against the flat side of the shaft. *Take note of the direction with which each pulley was installed below and wrap the 118 teeth belt around both pulleys before simultaneously installing them onto their respective shafts.

30. Slide ‘J4_mount2’ through the geared Nema14 motor, attach ‘j4_mount’ to the motor using 4 M3x8mm screws and secure a small 6mm bore pulley to the motor using one M3x5mm screw against the flat of the shaft, making sure that the pulley is as close to the body of the motor as possible.

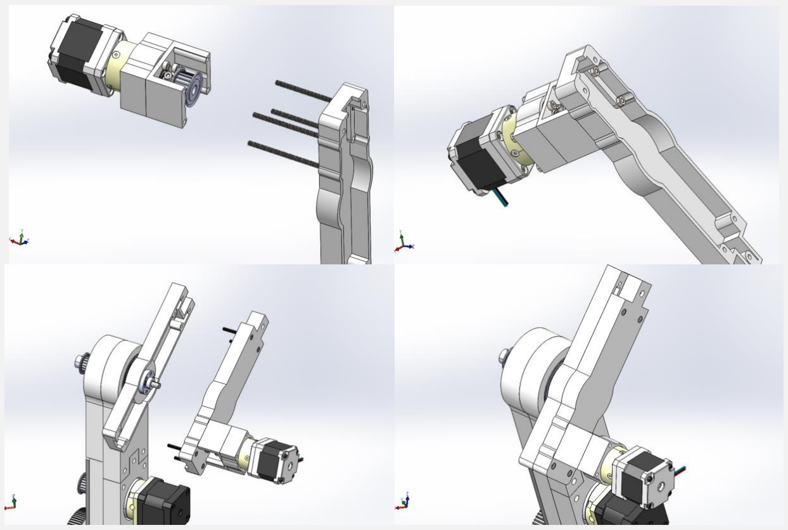
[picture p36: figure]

31. Attach the motor to ‘upper_arm_right_1’ using 4 M3x55mm threaded rods and 8 nuts after wrapping the 187 teeth belt around the pulley and attach ‘upper_arm_right_1’ to ‘upper_arm_left_1’ using 4 M3 nuts, two M3x30mm screws at the top side and two M3x25mm screws at the bottom side.

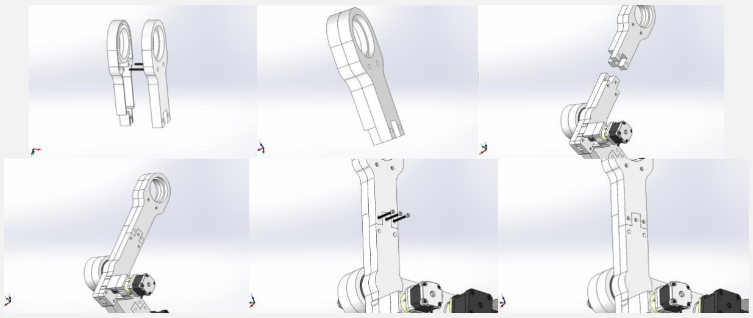
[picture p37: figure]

32. Attach ‘upper_arm_right_2’ to ‘upper_arm_left_2’ using two M3x30mm screws and two M3 nuts and attach this half to the rest of the arm using 3 M3x30mm screws and 3 M3 nuts.
33. Slide two 40mm bore bearings into their designated holes on the end of the assembled arm.

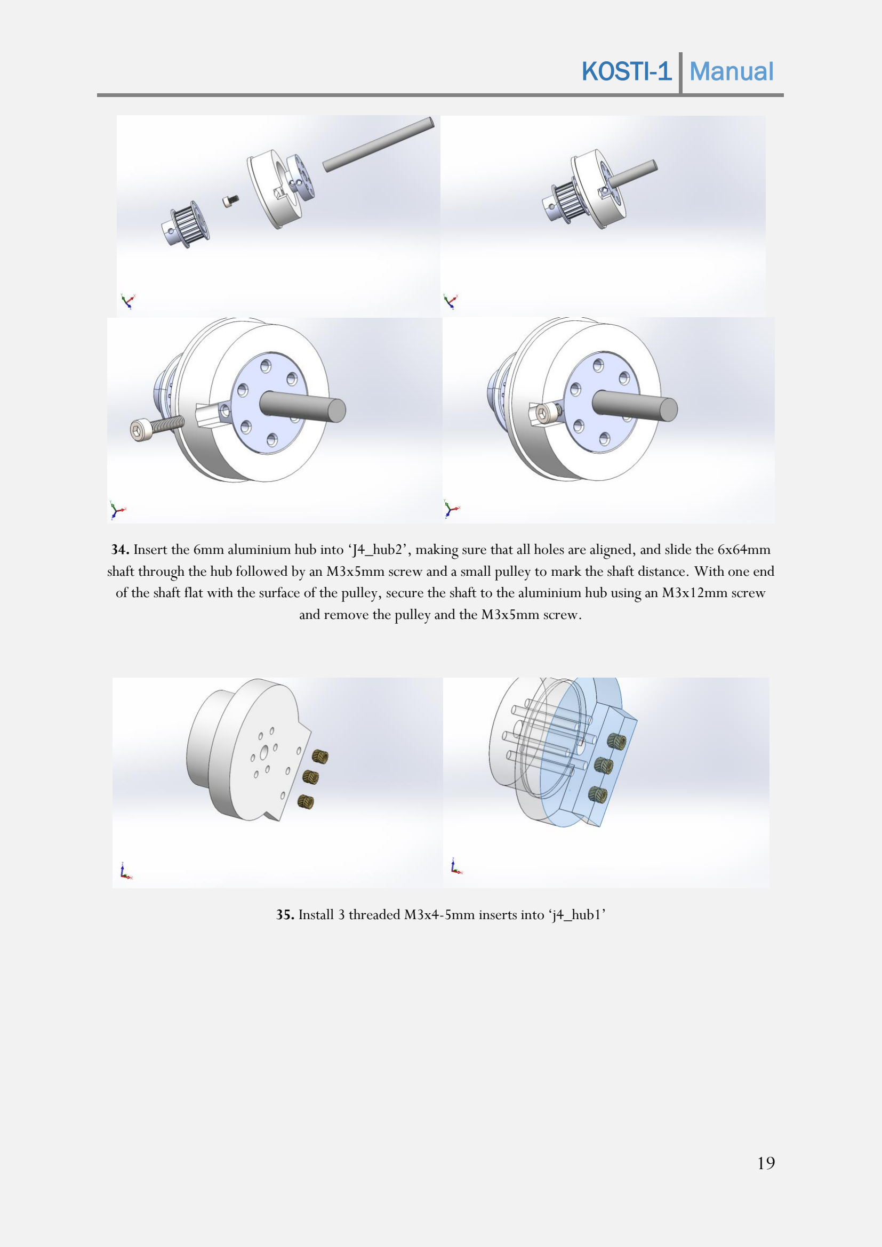
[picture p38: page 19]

34. Insert the 6mm aluminium hub into ‘J4_hub2’, making sure that all holes are aligned, and slide the 6x64mm shaft through the hub followed by an M3x5mm screw and a small pulley to mark the shaft distance. With one end of the shaft flat with the surface of the pulley, secure the shaft to the aluminium hub using an M3x12mm screw and remove the pulley and the M3x5mm screw.

### 35. Install 3 threaded M3x4-5mm inserts into ‘j4_hub1’

36. Align ‘j4_hub1’ and ‘link3’ as shown to mark the 3mm diameter holes that need to be drilled into ‘link3’ and attach ‘j4_hub1’ to ‘link3’ using 3 M3x12mm screws that go into the threaded inserts.
37. Attach ‘j4_hub1’ and ‘j4_hub2’ using 3 M3x30mm screws and secure a small 6mm bore pulley to the shaft using 1-2 M3x5mm screws, with the 187 teeth belt wrapped around the pulley.

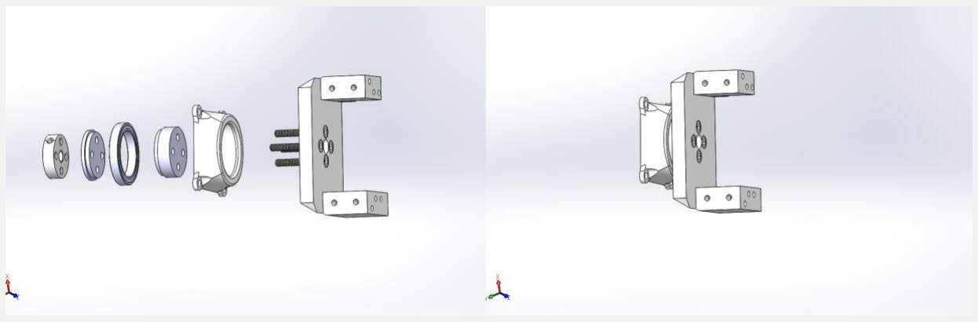
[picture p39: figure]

38. Attach the base of the end effector to the aluminium 5mm hub and two plastic hubs through the bearing housing and bearing as shown using 4 M3x20mm screws. The housing holds the outer ring of the bearing and the remaining 4 pieces should be secured to the inner ring.

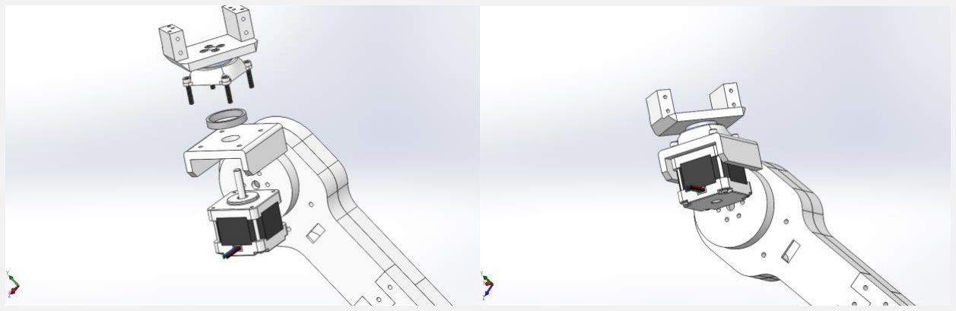
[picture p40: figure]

39. With the cylindrical piece called ‘bearing_housing2’ at the bottom, secure the rest of the housing and the bearing using 4 M3x16mm screws as shown.
40. Read the gripper’s original manual at anninrobotics.com/downloads for its remaining assembly instructions.

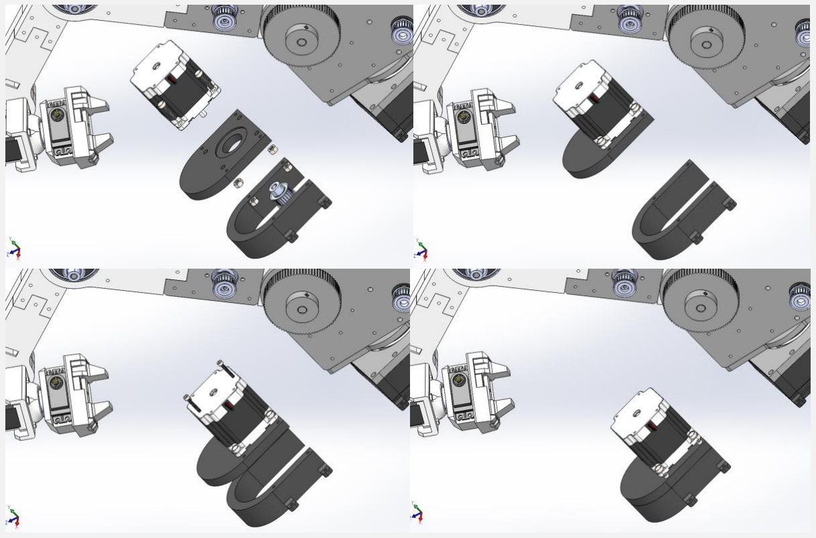
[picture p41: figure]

41. Secure a small 6mm bore pulley to the Nema23 motor with one M3x5mm screw against the flat of the shaft and with the pulley as close as possible to the body of the motor without the screw leaving the flat. Attach the motor to ‘J1_1’ using 4 M5x20mm screws and 4 M5 nuts and secure ‘j1_1’ to ‘j1_2’ using 4 M3x20mm screws.

Stepper Motor Wiring:

The Nema16, Nema14 and Nema17 motors use the DM32T drivers, and the Nema23 and Nema24 motors use the DM542T; the wiring for each is as follows:

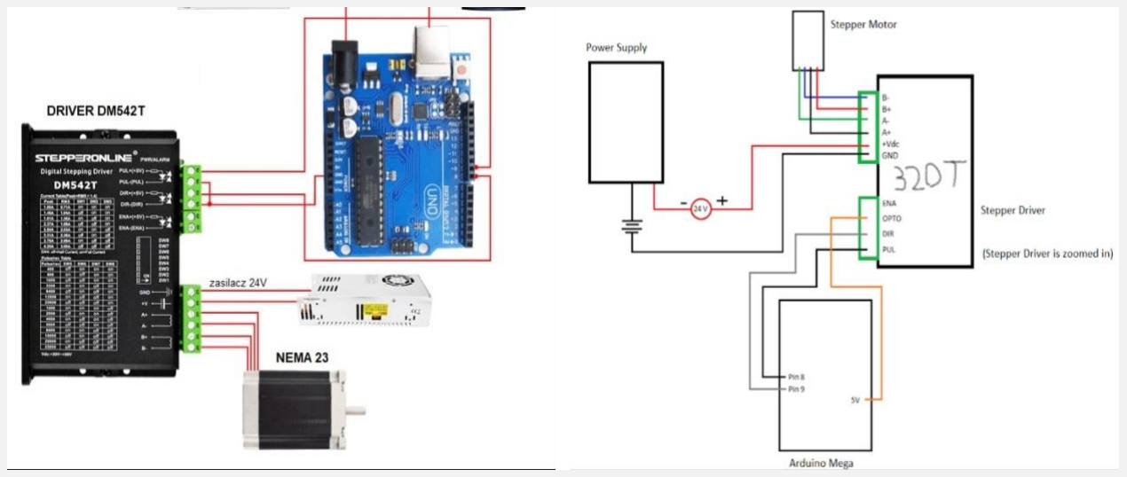
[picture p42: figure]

For the DM542T, two signal wires are connected to the Arduino for ‘pull’ and ‘direction’, two are connected to the Arduino’s ground, two to the DC power supply’s positive and negative and four are connected to the motor.

The order of the motor wires can be found on each motor’s manual, and the driver can be adjusted using the switches on its side to limit power draw, to turn on 5V signal mode and to adjust the step settings; quarter steps are recommended for the Nema24 motor, which is equal to 800 steps/revolution for 1.8o
per full step motors,
and 1600 steps/revolution are recommended for the Nema23. The DM32T driver doesn’t have a full step option, and can only support 400 steps/revolution settings. Note that gear/belt reductions and step fractions need to be taken into account while coding.

Most motors wires, including the servo’s, would need to be extended so they can comfortably reach the drivers in a spot clear from the arm, but wires that are too long can cause interference.

The second link has two holes for passing the wires for the gripper and j5 motor.

Servo Motor Wiring:

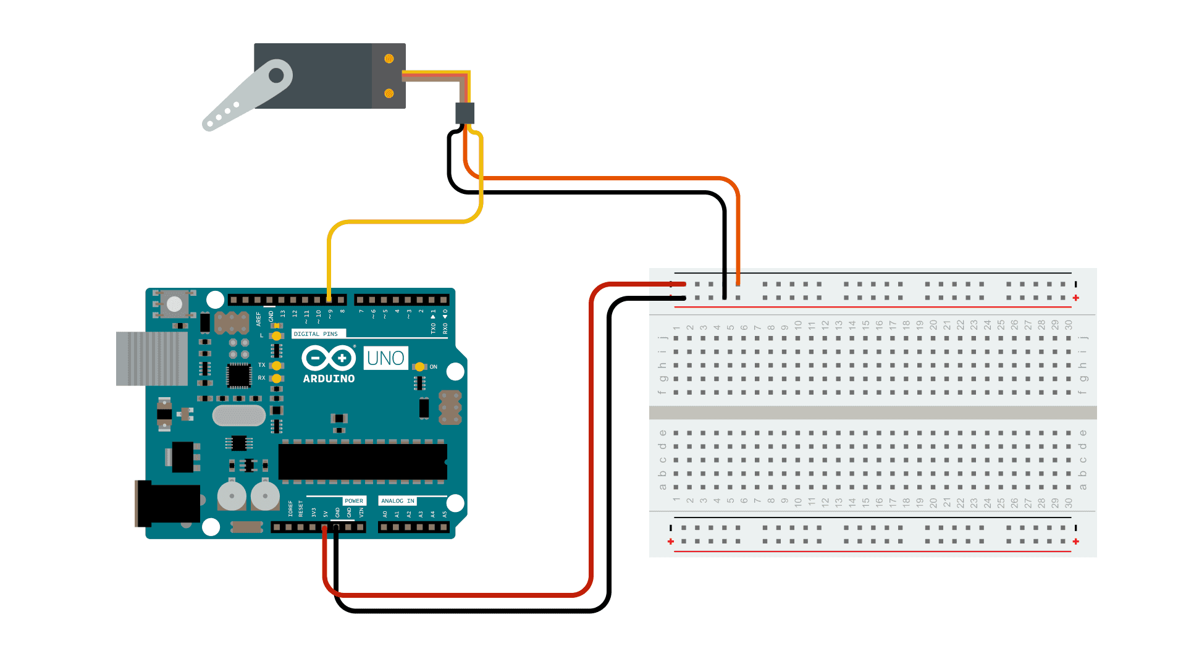
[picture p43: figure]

The servo has one wire for the signal and two for power; you should preferably power your servo from an external 5V source with more power, but remember that the Arduino, the external power source and the servo should still share a common ground.

Two example sketches can be found in the ‘example code’ folder.

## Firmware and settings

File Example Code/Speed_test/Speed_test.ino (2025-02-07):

// a set of manually written trajectories, one or multiple joints move during setup, or when a set of conditions is met by one or multiple other joints
// very important: this code assumes the same starting pose as in the video
// similarly, the servo grippers works when one or more conditions are met, note that this is a different gripper than the one in the assembly
// the accelstepper library allows for decelaration and acceleration for each joint, and the manually set paramaters for each motor account for the gear/belt reductions

//Stepper0 is the shoulder joint
//Stepper00 is the basejoint
//Stepper is the elbowjoint
//Stepper1 is the wristjoint
//Stepper2 is the shoulder joint
 
#include <AccelStepper.h>
#include <Servo.h>
 
//Defining pins
Servo myservo;
int pos = 0;

int Stepper0Pulse = 2;  // Pulse or step pin
int Stepper0Direction = 3;  // Direction pin
AccelStepper stepper0(1, Stepper0Pulse, Stepper0Direction);

int Stepper00Pulse = 4;  // Pulse or step pin
int Stepper00Direction = 5;  // Direction pin
AccelStepper stepper00(1, Stepper00Pulse, Stepper00Direction);

int StepperPulse = 6;  // Pulse or step pin
int StepperDirection = 7;  // Direction pin
AccelStepper stepper(1, StepperPulse, StepperDirection);

int Stepper1Pulse = 8;  // Pulse or step pin
int Stepper1Direction = 9;  // Direction pin
AccelStepper stepper1(1, Stepper1Pulse, Stepper1Direction);

int Stepper2Pulse = 10;  // Pulse or step pin
int Stepper2Direction = 11;  // Direction pin
AccelStepper stepper2(1, Stepper2Pulse, Stepper2Direction);
 
void setup()
{  
  myservo.attach(12);
    for (pos == 90; pos >= 0; pos -= 1) { // goes from 90 degrees to 0 degrees
    // in steps of 1 degree
    myservo.write(pos);              // tell servo to go to position in variable 'pos'
    delay(15);
}

  stepper0.setMaxSpeed(400);
  stepper0.setAcceleration(100);

  stepper00.setMaxSpeed(400);
  stepper00.setAcceleration(100);

  stepper.setMaxSpeed(800);
  stepper.setAcceleration(400);

  stepper1.setMaxSpeed(800);
  stepper1.setAcceleration(400);
  stepper1.moveTo(-1400);

  stepper2.setMaxSpeed(100);
  stepper2.setAcceleration(50);
}
 
void loop()
{
    // If at the end of travel go to the other end
if (stepper0.currentPosition() == 0
&&  stepper1.currentPosition() == -600)
      stepper0.moveTo(600);

if (stepper0.currentPosition() == 0
&&  stepper1.currentPosition() == -600)
      stepper.moveTo(-2500);

if (stepper0.currentPosition() == 0
&&  stepper1.currentPosition() == -600)
      stepper00.moveTo(400);

if (stepper0.currentPosition() == 0
&&  stepper1.currentPosition() == -600)
      stepper2.moveTo(-100);

if (stepper0.currentPosition() == 600
&&  stepper.currentPosition()  == -2500)
     stepper0.moveTo(0);

if (stepper0.currentPosition() == 600
&&  stepper.currentPosition()  == -2500)
     for (pos == 0; pos <= 90; pos += 1) { // goes from 0 degrees to 90 degrees
    // in steps of 1 degree
    myservo.write(pos);              // tell servo to go to position in variable 'pos'
    delay(15);
};

if (stepper0.currentPosition() == 600
&&  stepper.currentPosition()  == -2500)
     stepper.moveTo(0);

if (stepper0.currentPosition() == 600
&&  stepper.currentPosition()  == -2500)
     stepper1.moveTo(0);

if (stepper0.currentPosition() == 600
&&  stepper.currentPosition()  == -2500)
     stepper00.moveTo(0);

if (stepper0.currentPosition() == 600
&&  stepper.currentPosition()  == -2500)
     stepper2.moveTo(0);

    stepper0.run();
    stepper00.run();
    stepper.run();
    stepper1.run();
    stepper2.run();
}

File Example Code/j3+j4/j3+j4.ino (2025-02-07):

// Make a single stepper bounce from one limit to another
 
#include <AccelStepper.h>
 
//Defining pins
int StepperPulse = 6;  // Pulse or step pin
int StepperDirection = 7;  // Direction pin
AccelStepper stepper(1, StepperPulse, StepperDirection);
int Stepper1Pulse = 8;  // Pulse or step pin
int Stepper1Direction = 9;  // Direction pin
AccelStepper stepper1(1, Stepper1Pulse, Stepper1Direction);
 
void setup()
{  
  // Change these to suit your stepper if you want
  stepper.setMaxSpeed(400);
  stepper.setAcceleration(30);
  stepper.moveTo(-2000);
  stepper1.setMaxSpeed(400);
  stepper1.setAcceleration(30);
  stepper1.moveTo(-2000);
}
 
void loop()
{
    // If at the end of travel go to the other end
if (stepper.currentPosition() == -2000)
      stepper.moveTo(0);
      
    stepper.run();

if (stepper1.currentPosition() == -2000)
      stepper1.moveTo(0);

    stepper1.run();
}
